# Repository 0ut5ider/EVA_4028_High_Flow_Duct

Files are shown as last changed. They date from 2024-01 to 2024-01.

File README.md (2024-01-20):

# 4028 High Flow Duct for EVA toolhead

This is a modified duct for the EVA 4028 Fan Duct.
It optimizes the fan flow to achieve higher flow at the exit point at the nozzle.

This is comparison between the current EVA 4028 duct design and the new modified duct.
In the tests I redirect the flow of one of the horns of the nozzle duct, so as to only measure the flow from one side.

**Duct A** - The current design shows a range flow velocity range between 3.4 to 3.9 m/s.   
**Duct B** - The new design shows a range or flow velocity between 4.2 to sometims up to 4.8 m/s at some spots.

I am aware that the flow measurement is not consistent and varies since I'm not holding the anemometer in exactly the same spot every time.     
Chaging the average flow speed from 3.65 m/s to 4.5 m/s would certanly benefit some users.
If nothing else, you can run the fan at a lowe rpm and hence lower noise.   

https://github.com/0ut5ider/EVA_4028_High_Flow_Duct/assets/88666133/834bde17-1405-4503-b53a-58a323b9f26b

## Visual comparison of the differences

This is the duct you're familiar with from the EVA project
https://main.eva-3d.page/heat_insert/cooling_inlet/40mm/



The modifications are the addition of a central piece behind the 4028 fan (and a few air splitters which also hold the central part in place). 



For the purposes of the testing I printed a Two-Horn nozzle duct as well as part of the EVA back piece which connects the fan duct to the nozzle duct.

https://github.com/0ut5ider/EVA_4028_High_Flow_Duct/assets/88666133/c6780624-e585-49d4-9ce4-8a394958fdb8

## Theory

The effective fan cross section area is area over which the blades move the air. For the 4028 fan this area is 681 mm^2.   
This comes from the full fan area created by duct the inner diameter of 38mm (which equals 1134mm^2), and from that we subtract the inner hub area created by the 24mm inner hub (which equals 452 mm^2)   
After the airflow is passes thgrough the fan, it expands in the large volume behind the fan. This causes a lot of turbulance back there since expansion happens suddenly. 
When the area increases, the pressure increases and more importantly flow velocity decreases ([Bernoulli's principle at work](https://en.wikipedia.org/wiki/Bernoulli%27s_principle) ). At the exit of the fan duct, the area restricts to 543 mm^2 (the two rectangular openings combined) so the pressure drops and velocity increases again. All these changes in pressure and velocity in one duct adds up to significant inefficiencies. 

The duct mod tries to reduce the amount of pressure and velocity changes throughout the duct. This results in better airflow.   
In order to good laminar flow, we must retain the fan area (681 mm^2) throughout the duct. That is where this internal piece comes into effect. It maintains the airflow area to roughtly 700 mm^2 cross sectional area.   
This increased laminar flow (with less turbulance) results in better flow at the nozzle.

## CAD

The STP file is available in the github repo.
This duct is a mod to the Heat Insert version of the EVA duct.

## Future Work

This is the first stab at improving the airflow through the duct. There may be further optimizations that can be made to the design. 
- optimize the shape of the inner wall to maintain equal distance all around
- a better way of maintaing airflow cross sectional area at the transition and flow split into the two openings of the duct end.

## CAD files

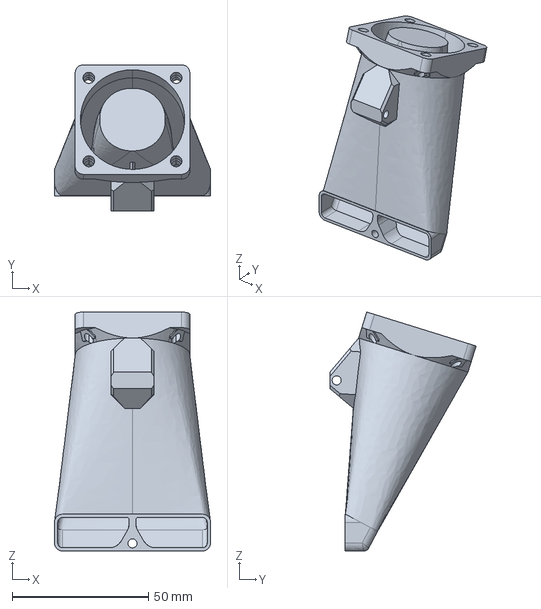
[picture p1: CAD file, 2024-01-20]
40mm Fan Inlet FI_5-rev2.stp
57.2 x 53.6 x 87.6 mm
